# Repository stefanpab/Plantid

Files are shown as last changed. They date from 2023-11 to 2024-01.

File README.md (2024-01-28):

# Welcome to Plantid

Plantid is an automatic watering system which works according the micro drip principle. The water will be pumped out of a watertank through a 3,7V pump.
With the help of a PVC-pipe the water will be transported to the water sprinklers - which are in the soil next to the plants. The amount of water 
coming out of the sprinkler can be adjusted by turning the head. In addition there is a web application which monitors moisture level, temperature,
the state of the pump and the current watering time. The standard watering time is 10 seconds but can always be changed manually by the user in the
web application. The watering system will start watering if the moisture value drops under 25% and will only water once a day to avoid overwatering 
the plant. In addition you can press the "EN" button to water manually. It will be watered as long as you press the button.

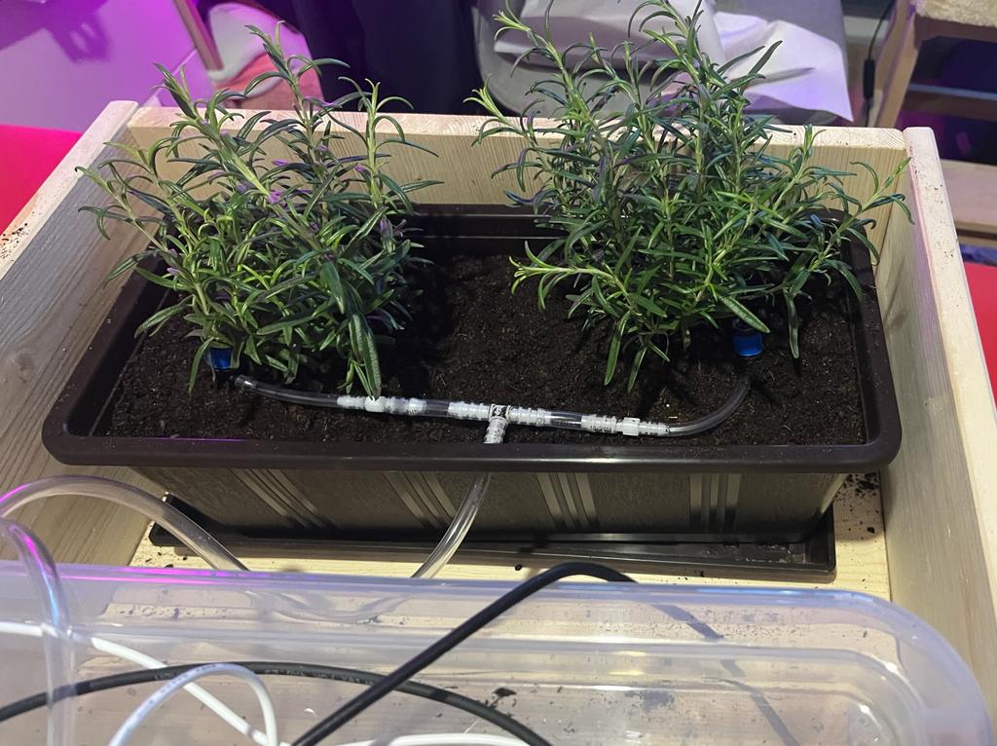
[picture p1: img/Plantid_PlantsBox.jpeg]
Plants placed in the box


## Content of the folders in this repo
The folders containing following information:
* _3D Case:_ all stl versions of the case for the pcb
* _Datasheets:_ all needed datasheeds for the project
* _Documentation:_ user manuals and documenation of plantid
* _Footprints:_ additional footprints needed for kicad 7.0
* _Kicad:_ schematics and PCB layout from Kicad 7.0
* _Software:_ arduino code and web application code
* _img:_ pictures of the project

## How to use Plantid
### Arduino IDE
To use plantid you have to first download the latest version of Arduino 1. !Important! You can't use the Arduino 2.0 application because the file 
upload manager you need for the project is not supported yet. You can Download it here: https://www.arduino.cc/en/software

### Arduino IDE additional managers
In addtion you need to download the file upload manager for esp32. 
1) Download ESP32FS-1.1 zip package: https://github.com/me-no-dev/arduino-esp32fs-plugin/releases/
2) You need to know your sketchbook location from your Arduino IDE. To find that, open the Arduino IDE and go to "File->Preferences"
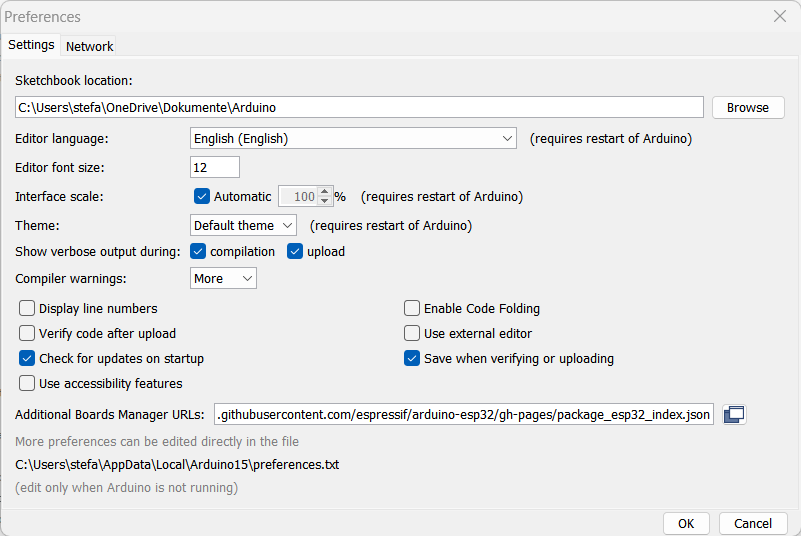
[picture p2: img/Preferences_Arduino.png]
Arduino Preferences

3) Go to the sketchbook location in your explorer and create a folder namened "tools"
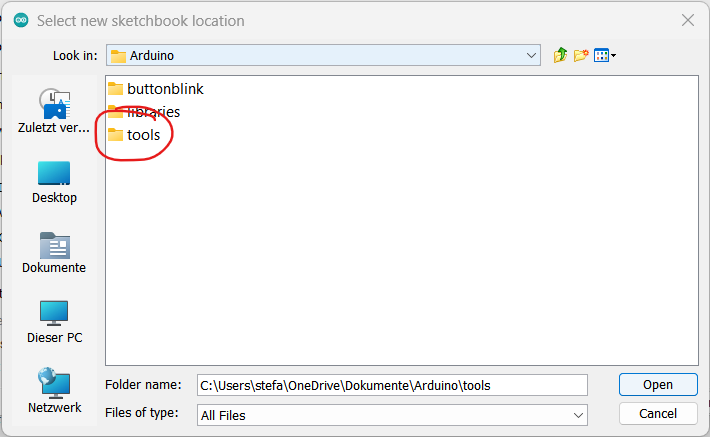
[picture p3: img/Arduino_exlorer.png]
Arduino exlporer Arduino explorer

4) Unzip the downloaded package and paste it into the tools folder
5) Restart the Arduino IDE
6) Now you will find under "Tools" the "ESP32 Sketch Data Upload" button

### Arduino IDE additional libraries
To make the project work you need to install some additional librarys. To install them click on Sketch->Include Library->Manage Libraries
Search for "ESP32Time" and press on install for following:
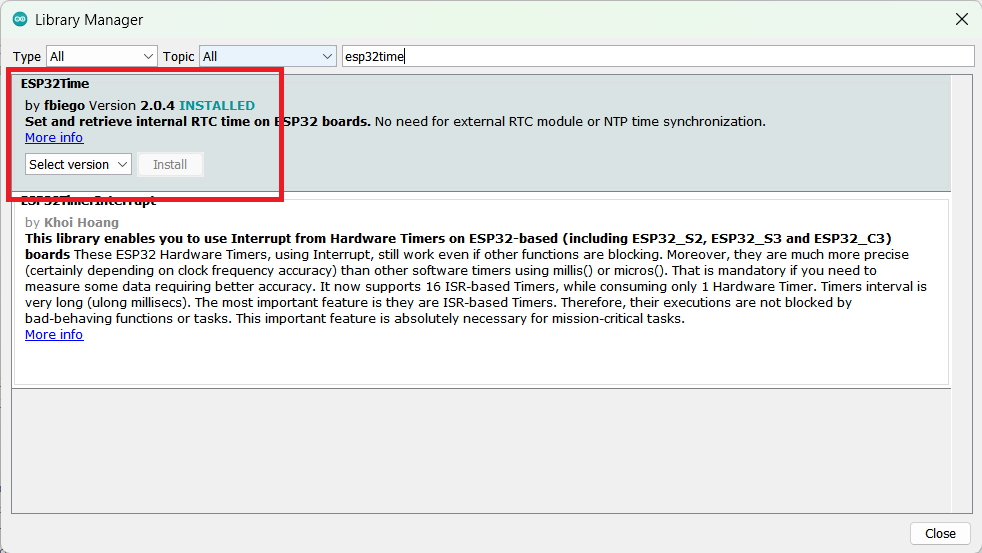
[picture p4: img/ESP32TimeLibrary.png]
ESP32 Time Library

You will need two additional libraries which are not in the Library Manager. To install them go to File->Preferences
Click on following button:
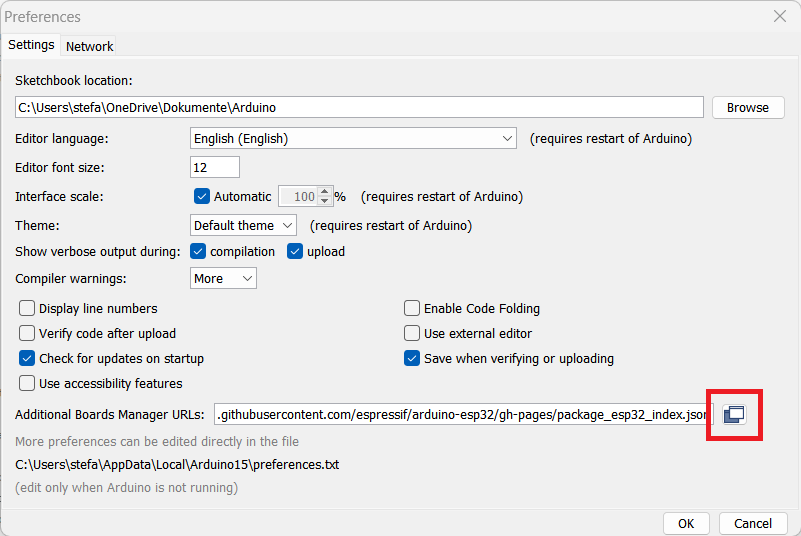
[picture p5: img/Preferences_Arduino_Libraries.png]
ESP32 Additional Libraries

Paste then the following line into it and press ok. With that line you will install the the AsyncTCP and the AsynchWebServer which are 
necassary to build the asynchrouns webserver.
"https://github.com/me-no-dev/ESPAsyncWebServer; https://github.com/me-no-dev/AsyncTCP"

### Code adjustments
To edit the arduino code, you have to open the /Software/plantid_sw/plantid_sw.ino file. 
You can make several changes in this file which best fits for your usecase. At line 48 and 49 you have to replace those wifi credentials with your 
home wife name and password. In addition you can open /Software/plantid_sw/data/index.html to change the web application. You can change the CSS, or 
removing for example the pump state to be seen on the web gui. After finishing the editing of those files, go back to the Arduino Software.
Plug in a micro USB cable into the ESP32 and into your computer. Now go to "tools" and press the "ESP32 Sketch Data Upload" button. In most cases you 
now have to press the boot button for two seconds. After you get the message "Done uploading" in the arduino console, the index.html is 
successfully be uploaded. Now you have to upload the code. Click on tools and apply following settings:
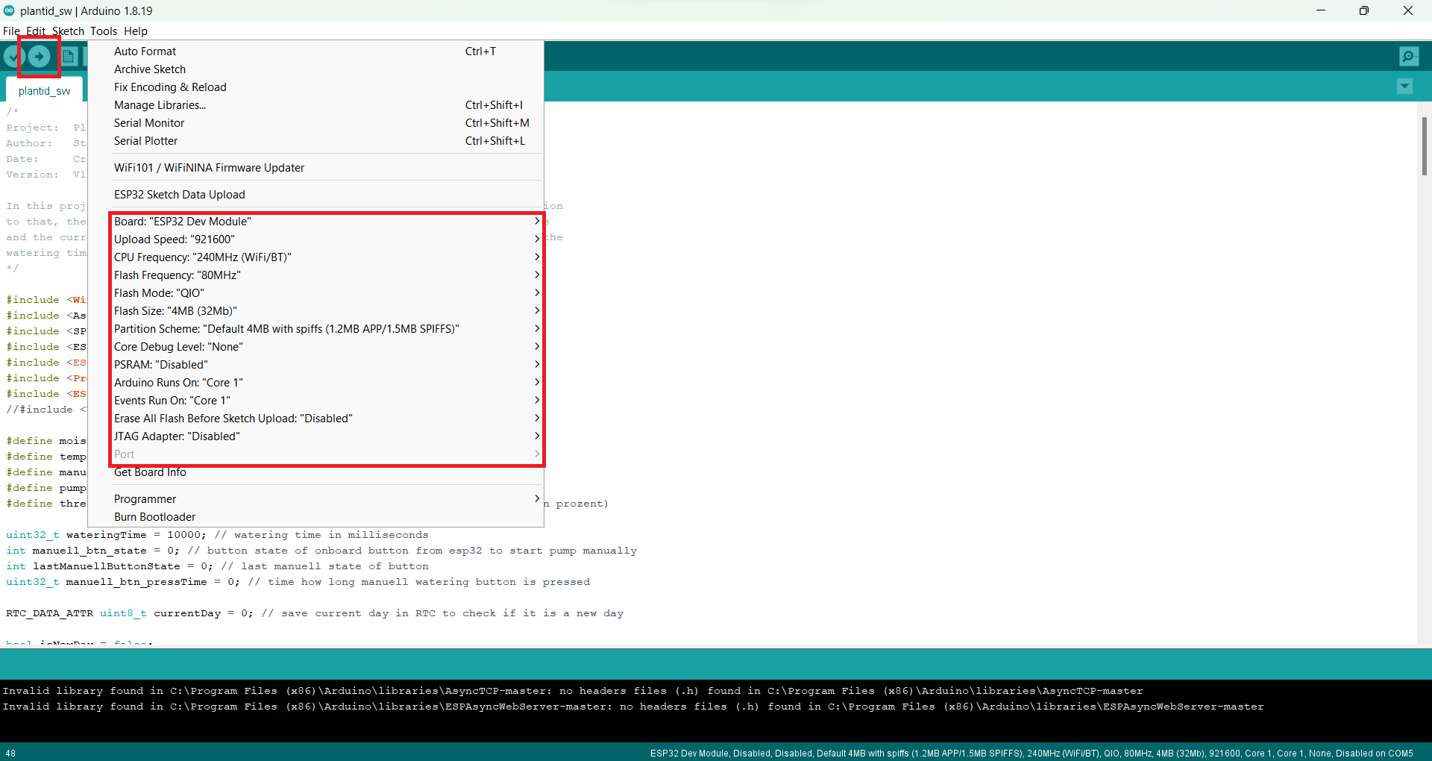
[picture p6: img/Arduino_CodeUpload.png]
Arduino code upload settings

Most important are Port and Board. Select "ESP32 Dev Module" as board and for the port the correct one where your ESP32 is plugged in. After selecting
the correct settings press the upload button (button in the red rectangle). In most cases it can be necassary to press the boot button again to 
successfully upload the code. After uploading the Code you can plug out the micro USB cable and screw the battery wires into the screw clamp.

### Web GUI
Now after uploading everything you can open the web gui by entering "plantid.local" in any internet explorer. You will now be able to see the current 
values of the watering system. In addition you can manually change the watering time by entering your needed time in seconds and confirming that by
pressing the "Change value" button.
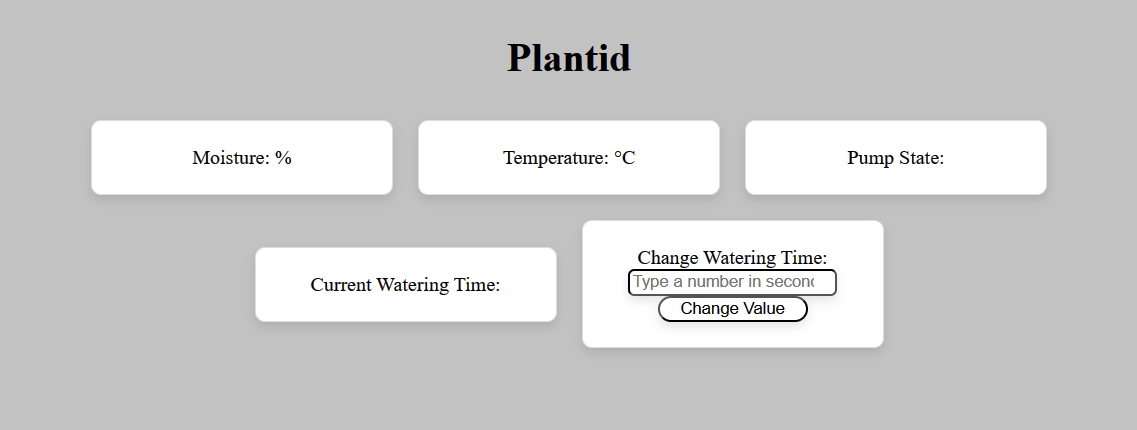
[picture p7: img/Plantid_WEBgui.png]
WEB GUI Plantid


### Hardware
Fill the tank with water but fill it no higher than the plant pot to avoid that the water won't stop floating after watering. Plant your plants into the 
pot and place the moisture sensor in the pot. For the best results from the sensor, bury the sensor as deep as possible under the plants. Scew the PCB into
the 3D case and connect the pump, sensor and battery to the pcb. Close the PCB and plug the pipes into the pump and the water tank.

## Documentation
In the documentation folder you can find the ibom file. This file shows you an interactive instruction how to solder the pcb with which components. In 
addition you have the components list as an csv file to know the order number of the required parts. Also you can find the circuit diagram, so you dont have 
to download KiCad to have a look at it. Last but not least you will also find the block diagram in there.

# Support
If you run into any problems or have any questions regarding the project, feel free to message me under my email: sa21b004@technikum-wien.at

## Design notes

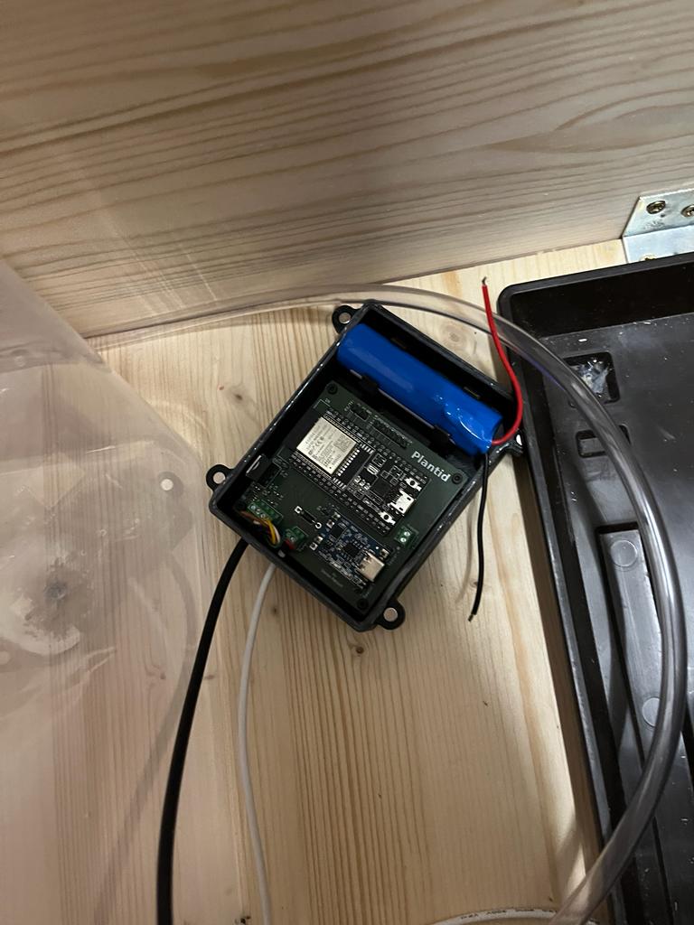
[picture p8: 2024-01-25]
img/Plantid_PCBinCase.jpeg

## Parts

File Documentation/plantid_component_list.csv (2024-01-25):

Reference | Value | Footprint | Datasheet | Digikey component number | Reichelt component number | Quantity
C1, C5, C7 | 100n | Capacitor_SMD:C_0603_1608Metric_Pad1.08x0.95mm_HandSolder | ~ | 1276-1000-1-ND |  | 3
C2, C3, C6 | 10u | Capacitor_SMD:C_0603_1608Metric_Pad1.08x0.95mm_HandSolder | ~ | 1276-1038-1-ND |  | 3
C4 | 1u | Capacitor_SMD:C_0603_1608Metric_Pad1.08x0.95mm_HandSolder | ~ | 1276-1038-1-ND |  | 1
D1 | D | Diode_THT:D_DO-41_SOD81_P10.16mm_Horizontal | ~ |  | 1N 4001 | 1
H1-H4 | MountingHole | MountingHole:MountingHole_2.2mm_M2 | ~ |  |  | 4
J1 | SMT50 | 1x04 Connector:CONN_OSTVN04A150_OST | ~ | ED10563-ND |  | 1
J2 | Pump | 1x02 Connector:CONN_OSTVN02A150_OST | ~ | ED10561-ND |  | 1
J3 | Battery | 1x02 Connector:CONN_OSTVN02A150_OST | ~ | ED10561-ND |  | 1
J4 | Load Mod r | Connector_PinHeader_2.54mm:PinHeader_1x02_P2.54mm_Vertical | ~ |  | MPE 087-1-002 | 1
J5 | Load Mod l | Connector_PinHeader_2.54mm:PinHeader_1x02_P2.54mm_Vertical | ~ |  | MPE 087-1-002 | 1
J6 | IO16-19 | Connector_PinHeader_2.54mm:PinHeader_1x06_P2.54mm_Vertical | ~ |  | MPE 087-1-006 | 1
J7 | RX/TX | Connector_PinHeader_2.54mm:PinHeader_1x03_P2.54mm_Vertical | ~ |  | MPE 087-1-003 | 1
J8 | Spacer r | Connector_PinHeader_2.54mm:PinHeader_1x02_P2.54mm_Vertical | ~ |  | MPE 087-1-002 | 1
J9 | Spacer l | Connector_PinHeader_2.54mm:PinHeader_1x02_P2.54mm_Vertical | ~ |  | MPE 087-1-002 | 1
Q4 | BSH108 | BSH108:SOT23_NXP | BSH108 | 1727-4925-2-ND |  | 1
R1 | 10k | Resistor_SMD:R_0603_1608Metric_Pad0.98x0.95mm_HandSolder | ~ | RMCF0603FT10K0CT-ND |  | 1
U1 | WE-TVS-824015043 | Package_TO_SOT_SMD:SOT-23-6_Handsoldering | https://www.we-online.com/components/products/datasheet/824015043.pdf | D1213A-04SO-7DITR-ND |  | 1
U2 | LD1117S33TR_SOT223 | LD1117V33:TO255P1020X450X1968-3 | http://www.st.com/st-web-ui/static/active/en/resource/technical/document/datasheet/CD00000544.pdf | 497-1491-5-ND |  | 1
U3 | ESP32-DEVKITC-32D | ESP32-DEVKITC-32D:MODULE_ESP32-DEVKITC-32D |  | 1965-1000-ND |  | 1

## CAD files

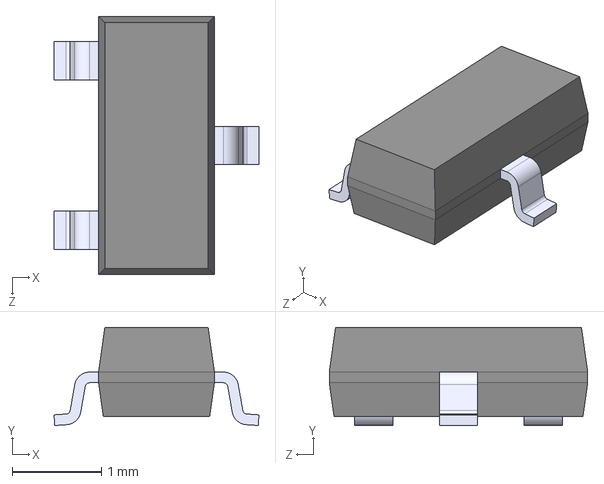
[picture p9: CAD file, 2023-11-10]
Footprints/BSH108_215/BSH108_215.step
2.30 x 1.10 x 2.90 mm

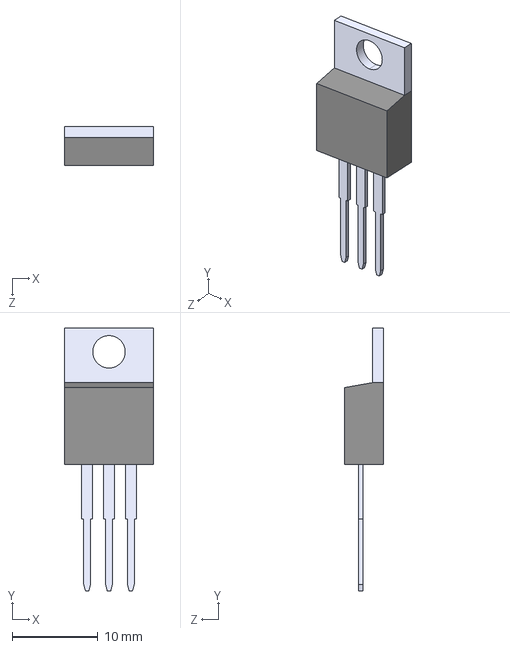
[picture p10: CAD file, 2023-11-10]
Footprints/LD1117V33/LD1117V33.step
10.3 x 30.6 x 4.57 mm

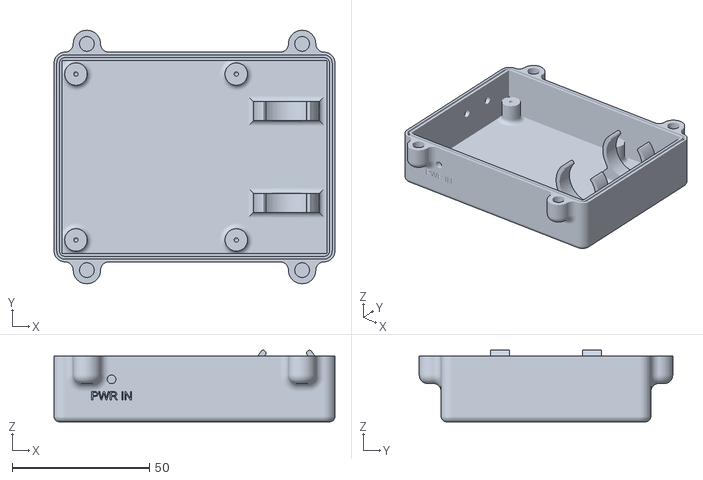
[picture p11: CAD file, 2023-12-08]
3D-Case/plantid_bottom_case_v5.0.stl
102.5 x 92.5 x 26.2

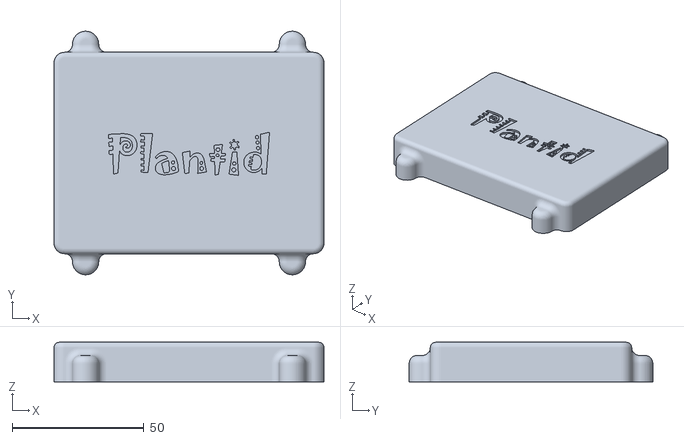
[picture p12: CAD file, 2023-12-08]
3D-Case/plantid_top_case_v5.0.stl
102.5 x 92.5 x 15.0

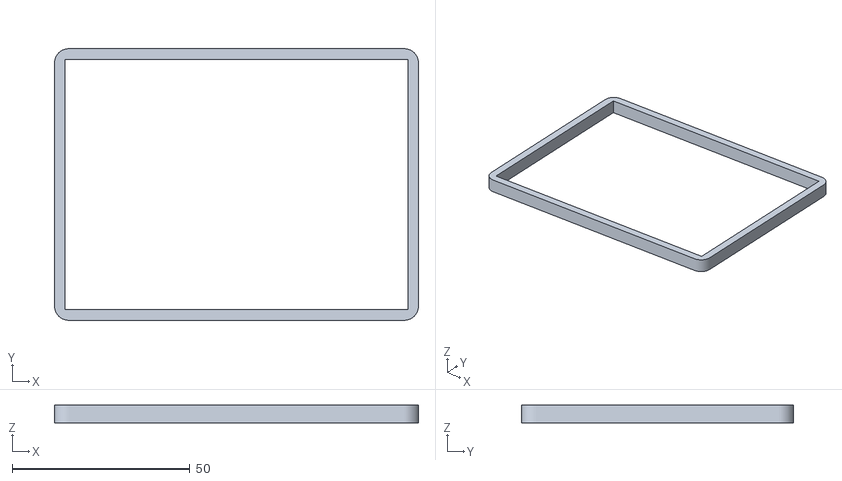
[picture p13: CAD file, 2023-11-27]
3D-Case/plantid_silicon_form_v1.0.stl
102.5 x 76.5 x 5.00

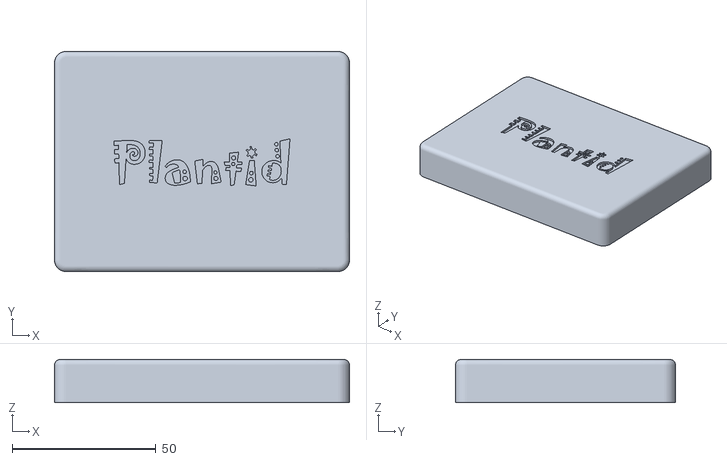
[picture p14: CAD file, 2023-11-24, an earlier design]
3D-Case/plantid_top_case_v1.0.stl
102.5 x 76.5 x 15.0

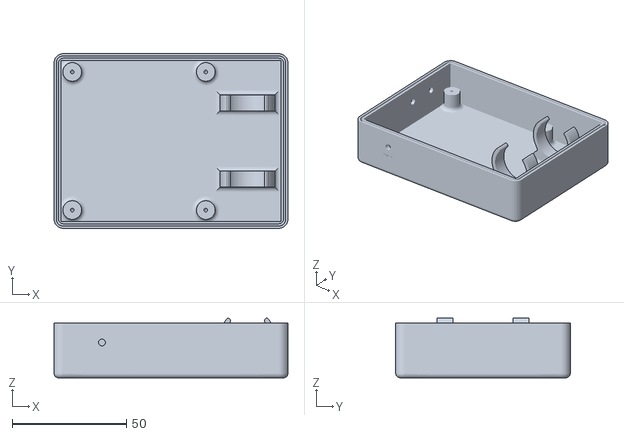
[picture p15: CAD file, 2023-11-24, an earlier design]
3D-Case/plantid_bottom_case_v1.0.stl
102.5 x 76.5 x 26.2

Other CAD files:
3D-Case/plantid_bottom_case_v4.0.stl
3D-Case/plantid_top_case_v3.0.stl
3D-Case/plantid_top_case_v4.0.stl
3D-Case/plantid_bottom_case_v2.0.stl
3D-Case/plantid_top_case_v2.0.stl

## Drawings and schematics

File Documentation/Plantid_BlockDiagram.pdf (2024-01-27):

# Case

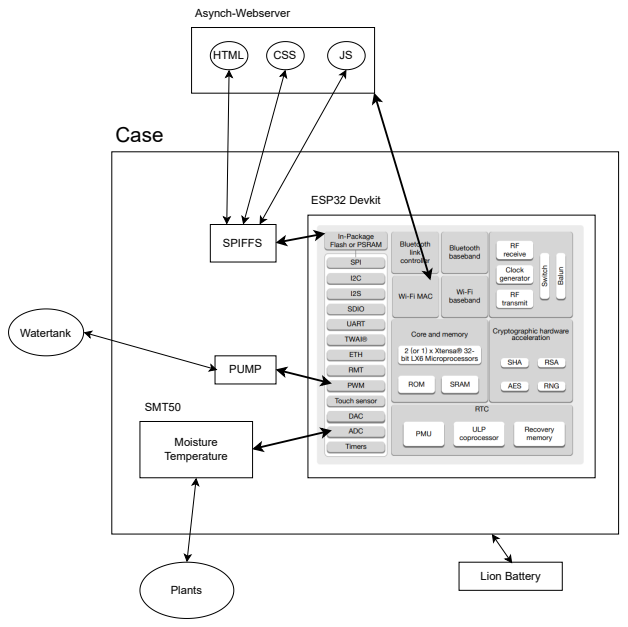
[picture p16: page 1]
SPIFFS; HTML; CSS; ESP32 Devkit; Moisture Temperature; SMT50; PUMP; Plants; Watertank; Asynch-Webserver; Lion Battery

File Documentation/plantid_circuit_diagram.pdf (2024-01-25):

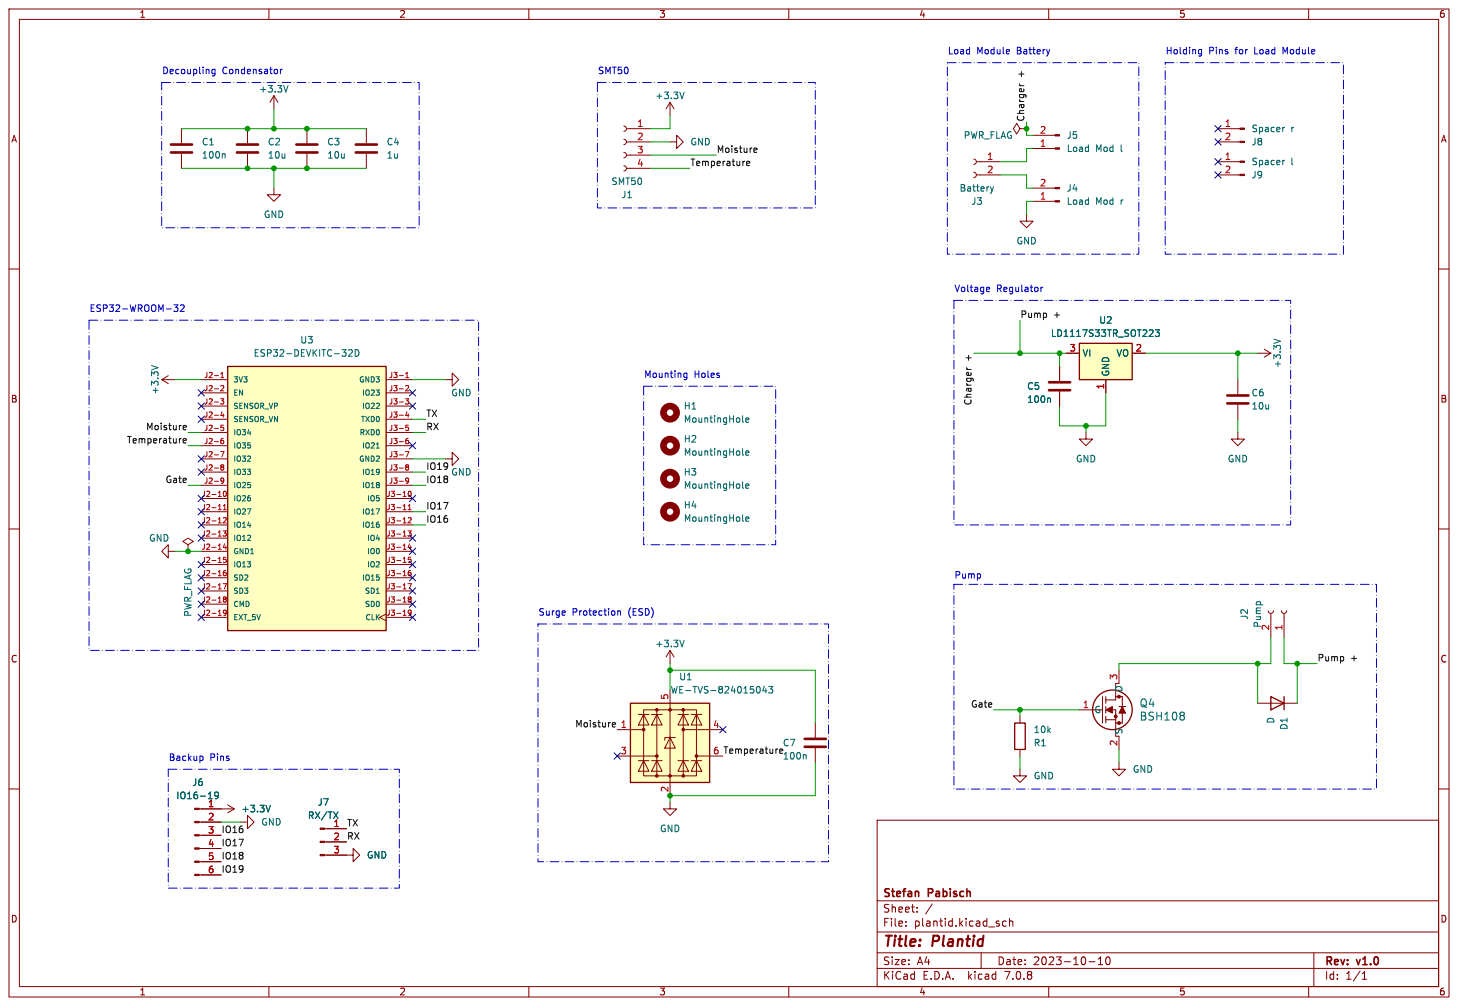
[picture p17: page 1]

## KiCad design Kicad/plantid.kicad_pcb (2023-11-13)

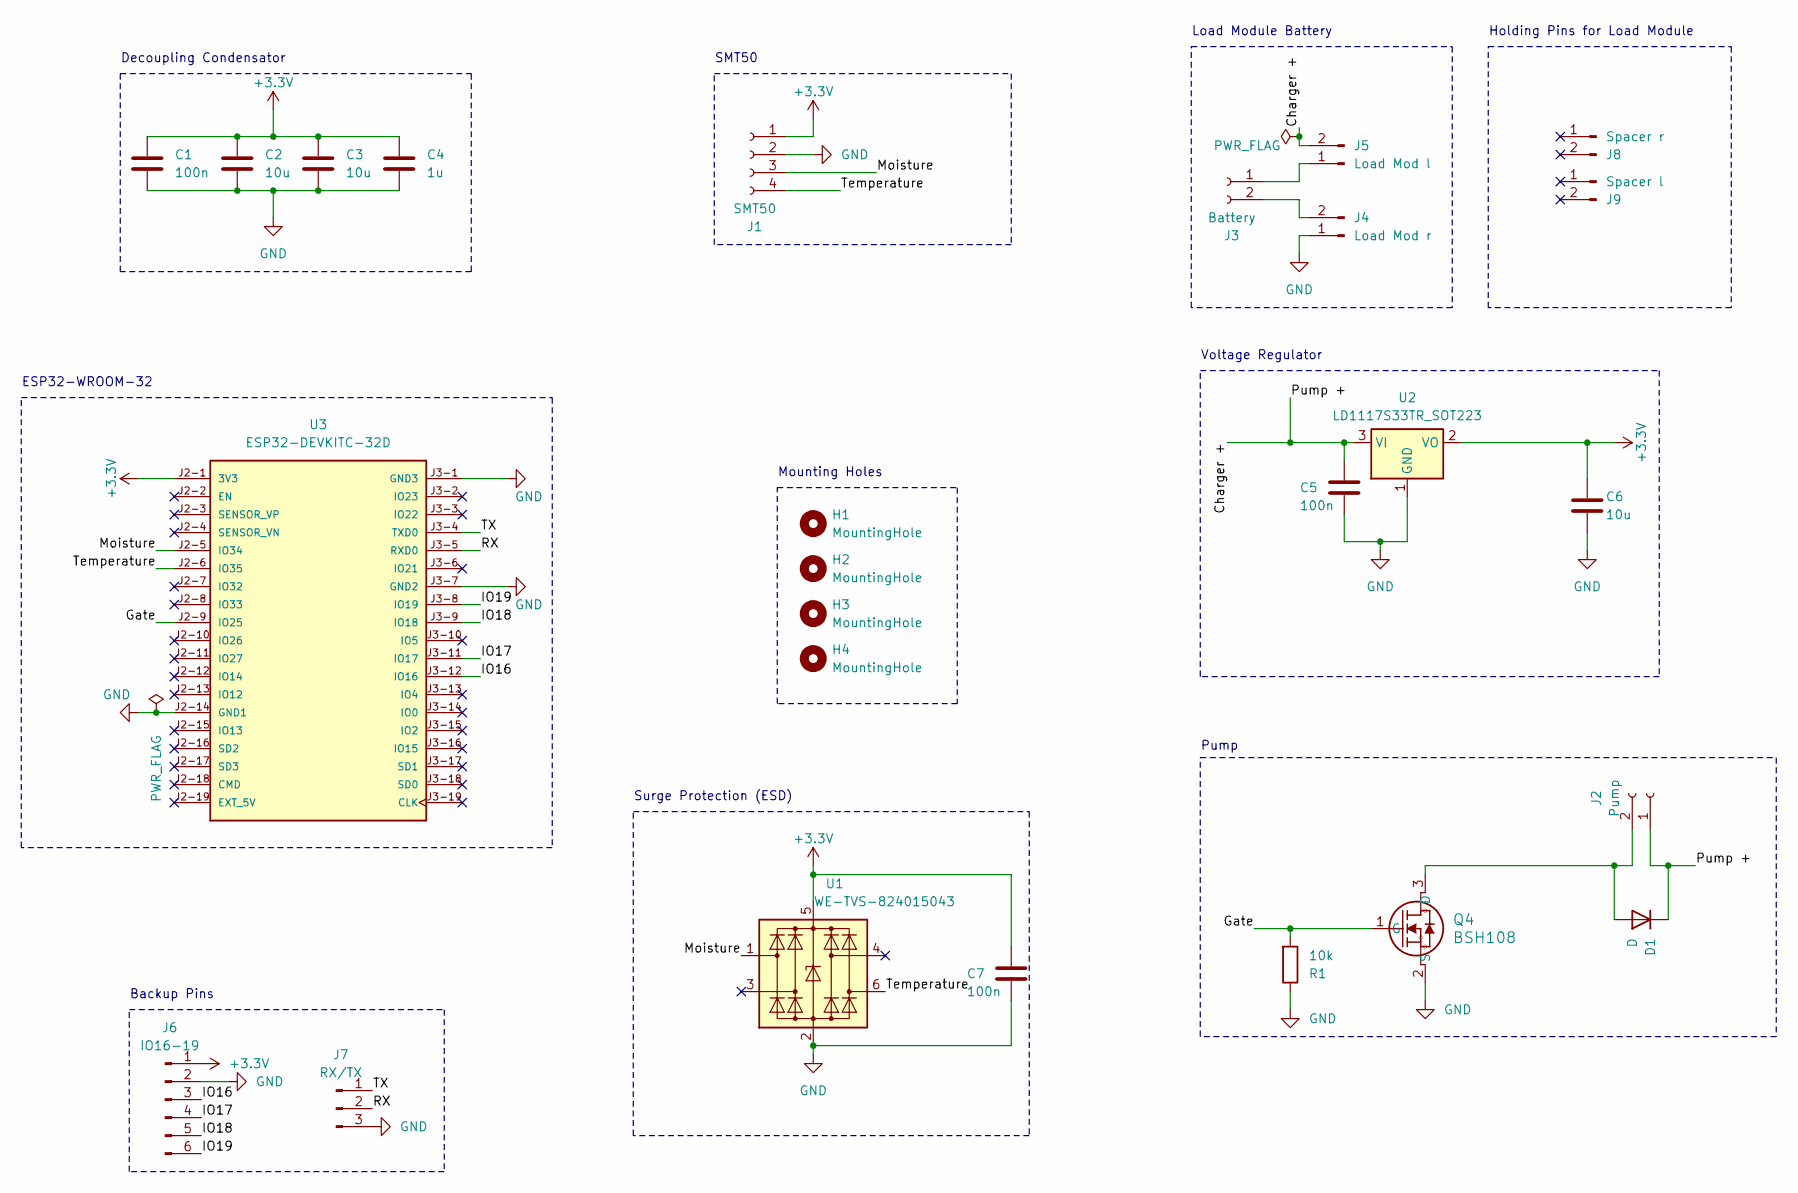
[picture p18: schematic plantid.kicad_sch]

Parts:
C1, C5, C7: 100n; C_0603_1608Metric_Pad1.08x0.95mm_HandSolder; Digikey 1276-1000-1-ND
C2, C3, C6: 10u; C_0603_1608Metric_Pad1.08x0.95mm_HandSolder; Digikey 1276-1038-1-ND
C4: 1u; C_0603_1608Metric_Pad1.08x0.95mm_HandSolder; Digikey 1276-1038-1-ND
D1: D; D_DO-41_SOD81_P10.16mm_Horizontal
H1, H2, H3, H4: MountingHole; MountingHole_2.2mm_M2
J1: SMT50; CONN_OSTVN04A150_OST; Digikey ED10563-ND
J2: Pump; CONN_OSTVN02A150_OST; Digikey ED10561-ND
J3: Battery; CONN_OSTVN02A150_OST; Digikey ED10561-ND
J4: Load Mod r; PinHeader_1x02_P2.54mm_Vertical
J5: Load Mod l; PinHeader_1x02_P2.54mm_Vertical
J6: IO16-19; PinHeader_1x06_P2.54mm_Vertical
J7: RX/TX; PinHeader_1x03_P2.54mm_Vertical
J8: Spacer r; PinHeader_1x02_P2.54mm_Vertical
J9: Spacer l; PinHeader_1x02_P2.54mm_Vertical
Q4: BSH108; SOT23_NXP; Digikey 1727-4925-2-ND
R1: 10k; R_0603_1608Metric_Pad0.98x0.95mm_HandSolder; Digikey RMCF0603FT10K0CT-ND
U1: WE-TVS-824015043; SOT-23-6_Handsoldering; Digikey D1213A-04SO-7DITR-ND
U2: LD1117S33TR_SOT223; TO255P1020X450X1968-3; Digikey 497-1491-5-ND
U3: ESP32-DEVKITC-32D; MODULE_ESP32-DEVKITC-32D; PARTREV V4; Digikey 1965-1000-ND

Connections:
+3.3V: C1.2, C2.2, C3.2, C4.2, C6.1, C7.1, J1.1, J6.1, U1.5 (VBUS), U2.2 (VO), U3.J2-1 (3V3)
/Charger +: C5.1, D1.1 (K), J2.1, J5.2, U2.3 (VI)
/Gate: Q4.1 (G), R1.2, U3.J2-9 (IO25)
/IO16: J6.3, U3.J3-12 (IO16)
/IO17: J6.4, U3.J3-11 (IO17)
/IO18: J6.5, U3.J3-9 (IO18)
/IO19: J6.6, U3.J3-8 (IO19)
/Moisture: J1.3, U1.1 (I/O1), U3.J2-5 (IO34)
/RX: J7.2, U3.J3-5 (RXD0)
/TX: J7.1, U3.J3-4 (TXD0)
/Temperature: J1.4, U1.6 (I/O4), U3.J2-6 (IO35)
GND: C1.1, C2.1, C3.1, C4.1, C5.2, C6.2, C7.2, J1.2, J4.1, J6.2, J7.3, Q4.2 (S), R1.1, U1.2 (GND), U2.1 (GND), U3.J2-14 (GND1), U3.J3-1 (GND3), U3.J3-7 (GND2)
unnamed: D1.2 (A), J2.2, Q4.3 (D)
unnamed: J3.1, J5.1
unnamed: J3.2, J4.2

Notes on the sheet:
SMT50
Backup Pins
ESP32-WROOM-32
Surge Protection (ESD)
Load Module Battery
Mounting Holes
Voltage Regulator
Decoupling Condensator
Holding Pins for Load Module
Pump

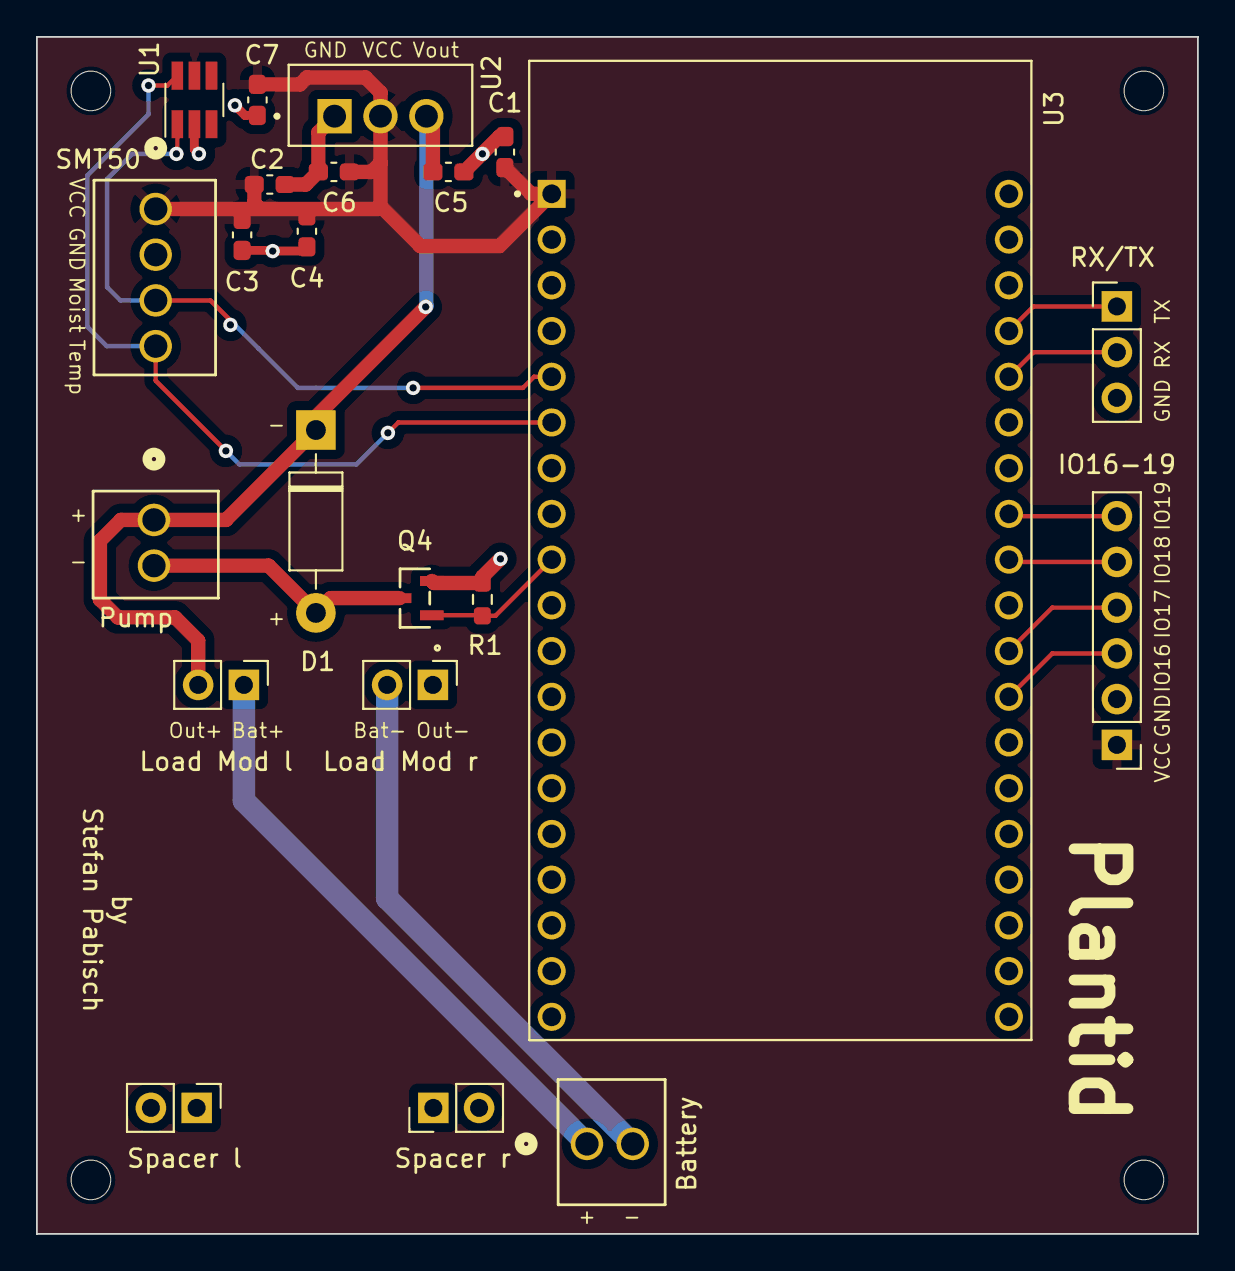
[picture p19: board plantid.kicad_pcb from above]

Board: 2 copper layers, 64.5 x 66.5 mm, 26 parts (0 on the bottom side), 15 nets.

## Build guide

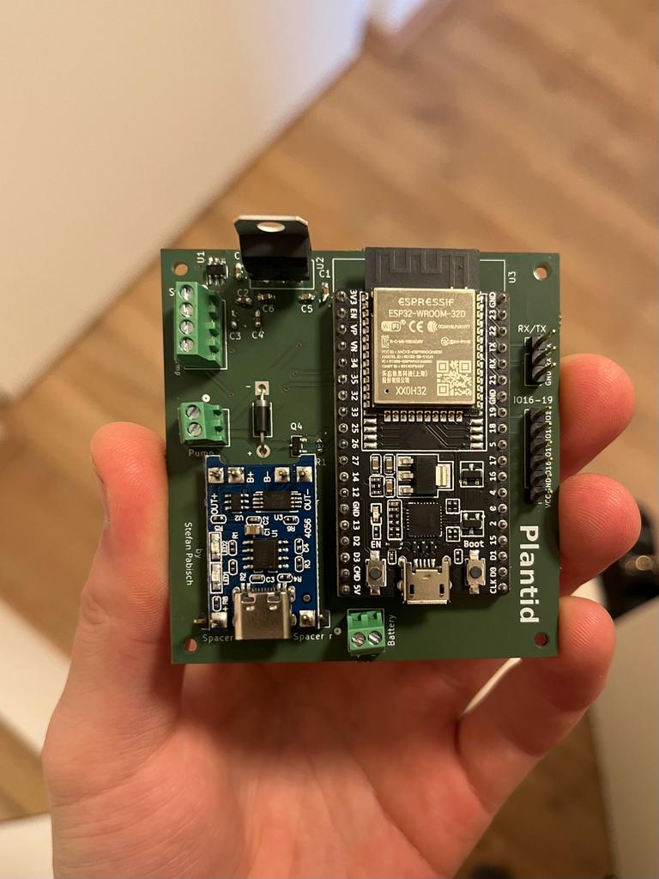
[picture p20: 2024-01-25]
img/Plantid_solderedPCB.jpeg

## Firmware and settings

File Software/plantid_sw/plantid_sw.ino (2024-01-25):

/*
Project:  Plantid - Automatic Watering for Plants
Author:   Stefan Pabisch (sa21b004@technikum-wien.at)
Date:     Created 19.04.2020 
Version:  V1.0
 
In this project it will be possible to automatically water your plants. In Addition
to that, there will be a web gui to monitor the temperature, moisture, pump state
and the current watering time. In the web gui it is possible to manually change the
watering time.
*/

#include <WiFi.h>
#include <AsyncTCP.h>
#include <SPIFFS.h>
#include <ESPAsyncWebSrv.h>
#include <ESP32Time.h>
#include <Preferences.h>
#include <ESPmDNS.h>

#define moisturePIN 34 // ADC PIN which reads the moisture value
#define temperaturePIN 35 // ADC PIN which reads the temperature value
#define manuell_PUMP 0 // ESP32 Button which manually starts the pump when it is pressed (EN button)
#define pumpPIN 25 // MOSFET PIN to activate pump
#define threshold 25.0 // threshold for moisture to start watering (threshhold in prozent)

uint32_t wateringTime = 10000; // standard watering time in milliseconds
int manuell_btn_state = 0; // button state of onboard button from esp32 to start pump manually, will be triggered when button is pressed
int lastManuellButtonState = 0; // last manual state of button
uint32_t manuell_btn_pressTime = 0; // time how long manuell watering button is pressed

RTC_DATA_ATTR uint8_t currentDay = 0; // save current day in RTC to check if it is a new day (0-31)

bool isNewDay = false; // bool variable to check if a new day is already reached
bool currentPumpState = false; // checks if pump is active at the moment or not

// Create AsyncWebServer object on port 80
AsyncWebServer server(80);

// ESP32Time rtc;
ESP32Time rtc(3600);  // offset in seconds GMT+1

// Create preferences
Preferences preferences;

// WIFI credentials -> change to yours if you use it
const char* ssid = "LifanHome";
const char* password = "nexapote2620!";

float moisture = 0; // save read moisture value as a float value to calculate
float temperature = 0; // save read temperature value as a float value to calculate

/*
 * This function handles if server cant be found.
 */
void notFound(AsyncWebServerRequest *request) {
  String url = request->url(); // get current url 
  int slashPos = url.indexOf("/"); // search for the first slash
  String file = url.substring(slashPos + 1); // save everything as string after a slash is found

  if ((SPIFFS.exists(file))) {
    request->send(SPIFFS, file); // send the saved file which is already in the spiffs
  } else {
    request->send(404, "text/plain", "No file in SPIFFS found"); // send and error code, that no spiffs is found
  }
}

/*
 * This function is to check which day it is right now so the plants will only be watered once a day.
 */
void getCurrentDay() {
  int day = rtc.getDay(); // get the current day
  if (day != currentDay) {
    isNewDay = true;
  } else {
    isNewDay = false;
  }
}

/*
 * This function is to read out the moisture from the SMT50 sensor. It will then be saved in a string which gets returned.
 */
String readMoisture() {
  // read value from adc pin and divide it through 1024.0 to convert it to a voltage value, has to be
  // diveded through 1024.0 bc else there would be a problem converting bc of different data types
  float moistvoltage = (analogRead(moisturePIN) / 1024.0);  
  moisture = ((moistvoltage * 50.0) / 3.0); // converting incoming voltage value in %, this formular is from the producer of the sensor itself
  String moistureVal = String(moisture);
  // this if is required to see if there was any problem converting or reading the value
  if (isnan(moisture)) {
    Serial.println("Could not read any moisture value!");
    return "";
  } else {
    return moistureVal;
  }
}

/*
 * This function is to read out the temperature from the SMT50 sensor. It will then be saved in a string which gets returned.
 */
String readTemp() {
  // read value from adc pin and divide it through 1024.0 to convert it to a voltage value, has to be
  // diveded through 1024.0 bc else there would be a problem converting bc of different data types
  float tempvoltage = (analogRead(temperaturePIN) / 1024.0);
  temperature = ((tempvoltage - 0.5) * 100.0); // converting incoming voltage value in °C
  String temperatureVal = String(temperature);
  // this if is required to see if there was any problem converting or reading the value
  if (isnan(temperature)) {
    Serial.println("Could not read any temperature value!");
    return "";
  } else {
    return temperatureVal;
  }
}

/*
 * This function is to check in which state the pump is.
 */
String readPumpState() {
  String pumpStr;
  // through this if the current pump state variable will be changed which is needed to display it on the web gui
  if (currentPumpState == true) {
    pumpStr = "Pump active";
  } else {
    pumpStr = "Pump inactive";
  }
  return pumpStr;
}

/*
 * This function will activate the pump and start the watering process. If the threshold from 25% is reached
 * and not already a new day is it will start the pump for standard 10 seconds. In addition it changes the pump
 * state during active pumping.
 */
void startPump() {
  delay(1000); // set a delay of one second to avoid errors
  digitalWrite(pumpPIN, LOW);
  if (moisture <= threshold && isNewDay == true) { // only water if the moisture is under 25% and already a new day is, else the plants would be over watered
    currentDay = rtc.getDay();
    Serial.println("Pump starts watering!");
    digitalWrite(pumpPIN, HIGH);
    currentPumpState = true;
    Serial.println(currentPumpState);
    delay(wateringTime);
    Serial.println("Pump finished watering!");
    digitalWrite(pumpPIN, LOW);
    currentPumpState = false;
    Serial.println(currentPumpState);
  }
}

/*
 * This function allows to manually water the plants though a button press
 */
void manualWatering() {
  // get current state of button to avoid conflicts
  manuell_btn_state = digitalRead(manuell_PUMP);

  // check if button is pressed or being pressed
  if (manuell_btn_state == HIGH && lastManuellButtonState == LOW) {
    manuell_btn_pressTime = millis();  // save time how long the user pressed the button to know how long the pump has to be active
  }

  // check if button is released
  if (manuell_btn_state == LOW && lastManuellButtonState == HIGH) {
    // check if the button is being pressed more then 500ms and not just pressed unintentional
    if (millis() - manuell_btn_pressTime >= 500) {
      digitalWrite(pumpPIN, HIGH); //start watering
      Serial.println("Pump starts watering!");
      currentPumpState = true;
    }
  }

  // refresh last state of button
  lastManuellButtonState = manuell_btn_state;

  // check if watering ready to stop
  if (manuell_btn_state == LOW) {
    Serial.println("Pump finished watering!");
    digitalWrite(pumpPIN, LOW);
    currentPumpState = false;
  }
}

void setup() {

  // Start preferences and set a standard value for the watering time to 10 seconds
  preferences.begin("plantid-pref", false); // name preferences to identify later when changing watering time manually by user
  wateringTime = preferences.getInt("wateringTime", 10000);

  // Serial port for debugging
  Serial.begin(115200);
  WiFi.mode(WIFI_STA); // set wifi mode

  
  // Connect to Wi-Fi
  WiFi.begin(ssid, password);
  while (WiFi.status() != WL_CONNECTED) {
    delay(1000);
    Serial.println("Connecting to WiFi..");
  }

  // Initialize mDNS so the user do not have to enter the web gui by the ip but instead with "plantid.local"
  if (!MDNS.begin("plantid")) {   // Set the hostname to "plantid.local"
    Serial.println("Error setting up MDNS responder!");
    while(1) {
      delay(1000);
    }
  }
  Serial.println("mDNS responder started");

  // Print ESP32 Local IP Address. only necassary if user wants to enter web gui by ip
  Serial.print("Local IP of ESP32: ");
  Serial.println(WiFi.localIP());

  // Initialize SPIFFS for saving the files into it
  SPIFFS.begin();

  // set sensors as input and pump as output. setting them as input if they are sensors and just getting data and as output if they execute any action
  pinMode(moisturePIN, INPUT);
  pinMode(temperaturePIN, INPUT);
  pinMode(pumpPIN, OUTPUT);
  pinMode(manuell_PUMP, INPUT);

  // Route for root / web page. This page will standard be opended when user opens web gui
  server.on("/", HTTP_GET, [](AsyncWebServerRequest * request) {
    request->send(SPIFFS, "/index.html");
  });

  // Route for temperature value. Temperature value will be sent to be displayed on the web gui
  server.on("/temperature", HTTP_GET, [](AsyncWebServerRequest * request) {
    request->send_P(200, "text/plain", readTemp().c_str());
  });

  // Route for moisture value. Moisture value will be sent to be displayed on the web gui
  server.on("/moisture", HTTP_GET, [](AsyncWebServerRequest * request) {
    request->send_P(200, "text/plain", readMoisture().c_str());
  });

  // Route for pump state. Pump State value will be sent to be displayed on the web gui
  server.on("/pumpState", HTTP_GET, [](AsyncWebServerRequest * request) {
    request->send_P(200, "text/plain", readPumpState().c_str());
  });

  // Route to get the current watering time, which is set up
  server.on("/getWateringTime", HTTP_GET, [](AsyncWebServerRequest *request){
    String json = "{\"wateringTime\":" + String(wateringTime) + "}";
    request->send(200, "application/json", json);
  });

  // Route to update the watering time, which got set by the user in the web gui
  server.on("/updateWateringTime", HTTP_POST, [](AsyncWebServerRequest *request){
    if(request->hasParam("wateringTime", true)){
      uint32_t newWateringTime = request->getParam("wateringTime", true)->value().toInt();
      wateringTime = newWateringTime;

      //save it to preferences
      preferences.putInt("wateringTime", wateringTime);
      
      request->send(200, "text/plain", "OK");
    } else {
      request->send(400, "text/plain", "Bad Request"); // for error detection if new watering time could be updated
    }
  });

  // if no server is found call not found function
  server.onNotFound(notFound);

  // Start server
  server.begin();

  // close preferences
  preferences.end();
}

void loop() {

  /*
   * Execute all functions in a loop 
   */
  readMoisture();
  getCurrentDay();
  startPump();
  readPumpState();
  manualWatering();
}

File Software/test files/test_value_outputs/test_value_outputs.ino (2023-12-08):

#define moisturePIN 34
#define temperaturePIN 35
#define pumpPIN 25

bool currentPumpState = false;
float moisture = 0;
float temperature = 0; 

String readMoisture() {
  float moistvoltage = (analogRead(moisturePIN)/1024.0);
  Serial.print("analog moist");
  Serial.println(analogRead(moisturePIN));
  moisture = ((moistvoltage*50.0)/3.0); //converting incoming voltage value in %
  String moistureVal = String(moisture);
  Serial.print("float moist: ");
  Serial.println(moisture);
  Serial.print("String moist: ");
  Serial.println(moistureVal);
  if (isnan(moisture)) {
    Serial.println("Could not read any moisture value!");
    return "";
  } else {
    return moistureVal;
  }
}

String readTemp() {
  float tempvoltage = (analogRead(temperaturePIN)/1024.0);
  Serial.print("analog temp");
  Serial.println(analogRead(temperaturePIN));
  temperature = ((tempvoltage-0.5)*100.0); //converting incoming voltage value in °C
  String temperatureVal = String(temperature);
  Serial.print("float temp: ");
  Serial.println(temperature);
  Serial.print("String temp: ");
  Serial.println(temperatureVal);
  if (isnan(temperature)) {
    Serial.println("Could not read any temperature value!");
    return "";
  } else {
    return temperatureVal;
  }
}

String readPumpState() {
  String pumpStr;
  if(currentPumpState = true) {
    pumpStr = "Pump active";
  } else {
    pumpStr = "Pump inactive";
  }
  return pumpStr;
}

void setup() {
  Serial.begin(115200);

  pinMode(moisturePIN, INPUT);
  pinMode(temperaturePIN, INPUT);
  pinMode(pumpPIN, OUTPUT);

  readMoisture();
  readTemp();
  readPumpState();
}

void loop() {
}

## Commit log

2023-11-17 fixed displaying temp and moist
    [plantid_sw.ino]
2023-11-24 added 3d files
    [plantid_bottom.stl, plantid_top.stl]
2023-11-27 added RTC clock
    [plantid_bottom_case_v1.0.stl, plantid_top_case_v1.0.stl]
2023-11-27 added new versions of the 3d model
    [plantid_bottom_case_v2.0.stl, plantid_silicon_form_v1.0.stl, plantid_top_case_v2.0.stl]
2023-12-08 added testfiles and some little fixes
    [plantid_bottom_case_v4.0.stl, plantid_bottom_case_v5.0.stl, plantid_top_case_v3.0.stl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]
2023-12-26 fixed an error with int
    [plantid_sw.ino]
2024-01-15 updated some changes
    set milliseconds to seconds in html.
    added mdns
    added wifimanager
    added manuell watering per gpio0
2024-01-15 added manuell button to water
2024-01-25 added docu files and commands in arduino file
    [plantid_component_list.csv]
